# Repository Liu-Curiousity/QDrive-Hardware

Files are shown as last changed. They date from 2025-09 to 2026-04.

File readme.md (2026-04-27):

 # QDrive-硬件部分
 
 - 软件部分参见： [QDrive-软件部分](https://github.com/Liu-Curiousity/QDrive-Software)

 ## 如何使用

- **对于动手能力不强的同学，我们也贴心的准备了焊接装配好的成品电机供大家直接购买：[QD4310电机](https://qdrive.com.cn/products/qd4310/)**

1. **制板**：

   - 从[Release](https://github.com/Liu-Curiousity/QDrive-Hardware/releases)页面下载制版文件(gerber)即可发给板厂生产(板厚1mm,层压顺序选文件中已有)。
   - 如果你恰好财力雄厚，可以一并下载BOM表和贴片坐标文件，让板厂直接帮你贴片。
   - 自己贴片的话，由于元器件排布紧凑，没有留下元件编号丝印，要麻烦你对照着源文件或者嘉立创的焊接辅助工具贴片啦。

2. **组装**：

   - 电机使用的是GB4310/PM4310电机，请自行购买，购买时选择裸电机即可，本驱动板自带编码器。
   - 按照下图所示装配：
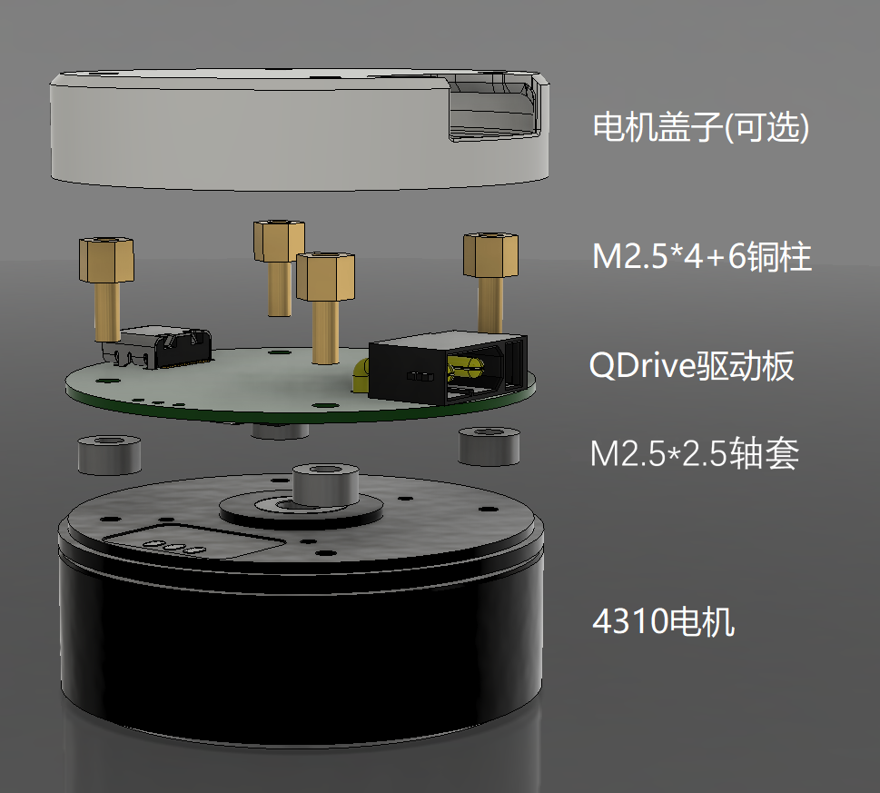
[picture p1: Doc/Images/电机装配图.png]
"电机装配图"
   
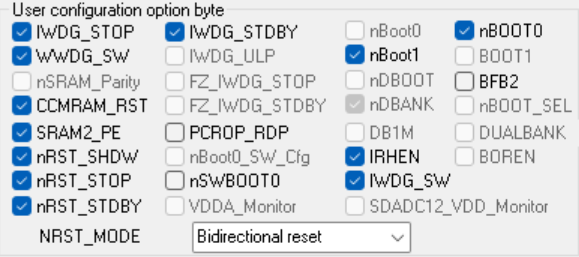
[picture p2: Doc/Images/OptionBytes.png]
"OptionBytes配置图"
   - 由于驱动板BOOT0引脚被CAN外设占用，需要通过配置单片机内部Option Bytes设置成软件boot，例如：使用ST-Link Utility工具配置Option Bytes，取消勾选nSWBOOT0选项。如图所示：

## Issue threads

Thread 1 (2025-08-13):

Boot0引脚没有被拉低，程序无法正常运行

cookieYBY, 2025-08-13:
我使用usb烧录了程序，但是程序无法运行，每次连接usb依旧是usb DFU下载模式

Liu-Curiousity, 2025-09-18:
你好，boot0引脚没有拉低确实是我的失误，可以通过ST-Link Utility工具配置Option Bytes，取消勾选nSWBOOT0选项解决，如图所示：
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
另外，两个采样电阻阻值为50mΩ，而BOM表中错误的将其写成了5m欧姆。这一错误已在最新Release中改正，给您带来不便。
感谢您的支持。

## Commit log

2025-02-06 Foc-Lite V1.0
    MCU:STM32F103CBU6
    Current Sensor:INA226
    Power:JW5026+RT9013
    BLDC Driver:FD6288
    CAN:SN65HVD232D
    Other:2xCAN,3xKEY,1xTYPE-C,1xSPI,1xABZ,1xIIC,1xUART,1xSWD,1xOLED
    [FOC-Lite.PrjPcb, PcbLib1.PcbLib, Schlib1.SchLib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]
2025-02-06 Foc-Lite V2.0
    MCU:STM32G431CBU6
    Current Sensor:AD8418
    Other:1xCAN,1xKEY,1xTYPE-C,1xSPI,1xABZ,1xSWD
    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
    [FOC-Lite.PrjPcb, Schlib1.SchLib, Sheet1.SchDoc]
2025-02-06 Foc-Lite V3.0
    Current Sensor:INA240
    BLDC Driver:DRV8300
    Other:1xCAN,1xKEY,1xSPI,1xSWD
    1.接口改为GH1.25,提升稳定性
    2.增加多个电容,试图改善开关时的VBAT电压波动
    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
    [FOC-Lite.PrjPcb, Sheet1.SchDoc]
2025-02-24 V3.1
    修复
    1. 修复CAN接口处错误的线序
    [Sheet1.SchDoc]
2025-03-20 FOC V3.1 for PM4310
    适配PM4310电机
    DRV8300驱动三桥
    双INA240端侧电流采样
    XT30(2+2)PB接口
    集成AS5047p编码器
    [FOC-Lite.PrjPcb, Sheet1.SchDoc]
2025-04-01 FOC V3.2 for PM4310
    1.修复INA240引脚定义错误的问题
    2.优化，电流采样添加前置抗混叠滤波器
    [FOC-Lite.PrjPcb, Sheet1.SchDoc]
2025-04-21 FOC V3.3for PM4310
    1.略微调整阻值容值即封装，为后续可能的SMT做准备
    2.将CAN终端电阻移至顶层，方便用户调整
    3.添加VBUS电压采样
    4.更改SWD烧录口为SH1.0接口
    [FOC-Lite.PrjPcb, Sheet1.SchDoc]
2025-04-21 FOC V4.0 for PM4310
    1.更换磁编码器为16位磁编KTH7823
    [Sheet1.SchDoc]
2025-05-03 FOC V4.1 for PM4310
    1.更换磁编码器为18位磁编MT6825
    [Sheet1.SchDoc]
2025-05-28 QDrive V5.0 for PM4310
    1.添加USB接口
    2.更改SWD接口为HC0.8
    3.添加TVS保护,包括SWD、USB、BAT
    4.优化VBAT采样并添加电容
    5.调整前置滤波器截止频率
    6.调整电机三相线焊盘形状方便焊接
    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
    [FOC-Lite.PrjPcb, PCB1.PcbDoc, Sheet1.SchDoc]
2025-07-17 QDrive V5.1 for PM4310
    1.调整SWD接口线序
    2.调整层顺序
    3.调整DP上拉电阻(VBUS->3.3V)
    [FOC-Lite.PrjPcb, PCB1.PcbDoc, Sheet1.SchDoc]
2025-07-25 添加开源资料
2025-09-18 修复:将错误的5mR采样电阻更改回50mR
    [PCB1.PcbDoc, Sheet1.SchDoc]
2025-09-18 调整开源资料
2026-01-14 QD4310 V6.0 for QD4310
    1.删除栅极0Ω电阻
    2.删除USB 0Ω电阻
    3.添加UART、PWM接口
    4.调整PCB布局
    5.更改编码器为MT6826S
    [FOC-Lite.PrjPcb, PCB1.PcbDoc, PcbLib1.PcbLib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]
2026-02-03 更换装配图片轴套高度
2026-04-27 QD4310 V6.1 for QD4310
    1.添加TXD二极管，支持一主多从通信
    [FOC-Lite.PrjPcb, PCB1.PcbDoc, Sheet1.SchDoc]
2026-05-28 QD4310 V6.2.0
    1.添加输入防反接和缓启动
    2.接口处添加更多的保护措施
    3.移除C口、螺纹孔接地
    4.添加版本控制
    5.添加MT6826S自校准引脚
    [PCB1.PcbDoc, Sheet1.SchDoc]
2026-05-29 QD4310 V6.2.1
    1.调整防反接和缓启动栅极电阻配置
    2.添加DCDC输入二极管
    3.删除MT6826S自校准引脚
    [FOC-Lite.PrjPcb, PCB1.PcbDoc, Sheet1.SchDoc]
